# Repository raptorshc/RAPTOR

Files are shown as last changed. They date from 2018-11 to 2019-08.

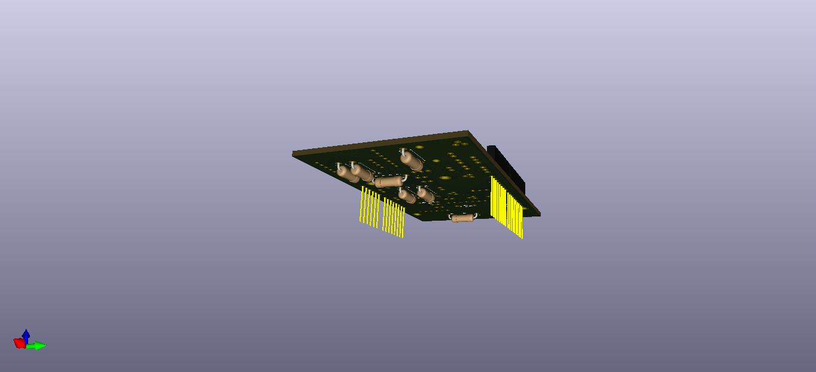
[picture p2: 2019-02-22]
hardware/phoneix_3D_bottom.png

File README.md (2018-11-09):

# RAPTOR

The Ram-Air Parafoil Targeted Object Return (RAPTOR) system is an autonomous payload designed for the simplification of high-altitude balloon payload recovery.

The project aims to alter final landing location by deflecting an attached parafoil. An Arduino Uno will control two servos that can trim the parafoil's brake lines to change course.  

This repository contains all of the flight code used for the project, flight data collected and analyzed, and simulation files.

## 1. Payload Design Overview

The RAPTOR payload will contain a few consistent components across all iterations of the payload. The box is a simple styrofoam box, the exterior of which will be modified to hold servo housings. Inside of the box is the electrical components and sensors to drive the payload. The "brain" of the payload is an Arduino, which will both interact with environmental sensors and drive the outputs.

Every iteration of the payload must be able to fly on regular balloon flights with little to no matenience needed. With these major design considerations in mind, we will set out to build a reliable and reusable payload that can easily be attached to any payload line.

With iterative design in mind, our goal is to make each step simple and elegant. Thus, if there is an easier solution to a problem, we will take that. The goal is to add complexity only as needed over time.

## 2. Flight Software Design

The requirements for flight software are to maintain accurate measurements from a variety of sensors, be able to determine and make the necessary corrections to the flight path, and facilitate the safe descent of the payload train to the ground when over the landing zone.

## 3. Payload Iterations

### **Kestrel**

'Kestrel' is part of the naming convention chosen for RAPTOR as it goes through various design and developement stages. Kestrel is the smallest raptor in North America, and was chosen to represent RAPTOR's first iteration, or the '0.5' version of the project.

Kestrel was designed and built to be a testing payload, where we could fly our environmental sensors, continuous servos and solenoids to test their reliability and power consumption on a high altitude flight.

![alt text](https://lh3.googleusercontent.com/1o9nY4RvOQGDZTQBY0d3M0oymKL5FPMcOie_QyGTn0_0s2nfabPlYtp4XrS53vgEl31j4T295NOKGKeISqotcockGwPX17MacXHBMp5uQQhCgSTBN3fivYLe4FH1sv7LIwD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 "Kestrel Payload")

![alt text](https://lh3.googleusercontent.com/uCabqWDjVLErh2zyCXdYhAvNTMVmv-jxHRv1PDopmbwNDc_ZhoJPY0nD8ILytu6s-EueVPPUXQ7v6TyP5FRkylkzkazS8X3QIo4R5wyPkX31q6gQq4APF3gKN9XSp_Dt44V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 "Kestrel Payload Interior Pre-Flight")

### **Falcon**

'Falcon' is the '1.0' version of the project. Falcon began when we made a completely new payload, with the plan of making our first real guided flight in mind. This is the first iteration of the payload with the parafoil attached, where all of the major flight goals for the project will be achieved. These goals include cut down, parafoil deployment, and guided descent.

![alt text](https://lh3.googleusercontent.com/08VQK_cJHctBsdPiarJFAllG-HUXjV4KG93Qopkh8PWqxyemp60GxGwwhsPvioKC6TSWX8pKGrXxwrKrk8XXFop7fkjdXXR2VQqJoVmNaJoeIMKOxXNGcJJWGRxl6ngI7tU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 "Falcon Payload with Parafoil Attached")

![alt text](https://lh3.googleusercontent.com/nTsq8ke9CdPrCzIl53acNa8SwdOpLuPSAk6aUb3CXytfzZnTHvZFV9xw1yQSyBJqHkr0cgnZ6tlVB8Kzcdpo9wiceyWq20kCEg2xDIhHhK3iLWAF6V_QYCNNu1fWfUKg2jk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 "Interior of Payload Pre-Flight")

![alt text](https://lh3.googleusercontent.com/qpwUnisi4AMiziGQZmHzRLYBiRqKub_Wn9nlaQfpf05oFm5Ekyx_R4OeDEhFKlS7zY80K_rwTjstmUsjaqJ_f78QGzWcw0SdS9lvnNbavl9Xdq8MnOOZnSqH13_WAorVAF_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 "Falcon Payload During Testing")

#### *Falcon Testing*

[Parafoil Testing with Fake Load](https://photos.google.com/share/AF1QipOYNhcAF_VKSpH8EsGm9p09tWBEW8-P44Ib4esdOKR__pPn4U8IfVZbABBhkwzWkA/photo/AF1QipNYzDb1yor08mGMRFYyb5cecjjzEDNiWGI3c_8m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)

[Cutdown and Parafoil Deployment Testing](https://photos.google.com/share/AF1QipOYNhcAF_VKSpH8EsGm9p09tWBEW8-P44Ib4esdOKR__pPn4U8IfVZbABBhkwzWkA/photo/AF1QipNU7GBOfcRdJiM-u27gPR9Wuxxhj8X0IvZJd2tQ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)

[Parafoil Brake Line Servo Test](https://photos.google.com/share/AF1QipOYNhcAF_VKSpH8EsGm9p09tWBEW8-P44Ib4esdOKR__pPn4U8IfVZbABBhkwzWkA/photo/AF1QipONFaLqnrI26lueZZusB5zbdpsSCUT9ZnrO1FEE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)

[Parafoil Controlled Deflection Testing](https://photos.google.com/share/AF1QipOYNhcAF_VKSpH8EsGm9p09tWBEW8-P44Ib4esdOKR__pPn4U8IfVZbABBhkwzWkA/photo/AF1QipOjYvH4XpJ5j8LqXkNAdmoZCI6CpGh4pJOYzDQ6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)

## 4. Flight Reports

### **KESTREL**

#### **April 21, 2018** (UAH Space Hardware Club BalloonSat Flight 75)

Our first flight took the Kestrel payload up to 100,000ft, where the components performed nearly perfectly, with only three measured failures of a solenoid. The following graphs are constructed from the data collected during the flight.

![alt text]( https://lh3.googleusercontent.com/BemMeG_wjjgEnfAlytIrjKeVrs0k2_3DL499e8Ap5Oft2oVPp0bTjnTxFLzm9G5_wCgSZQKKXPSeFjSZQ_YwVKfhydMyssC7hJiGl_VFefC5Ld4zEoicfH3cAaqB6fmjJgo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 "Pressure vs Time, with Solenoid Failure Markings")

![alt text](https://lh3.googleusercontent.com/KNZ6x_Vac3x1Pnvgrhe8NedKYn2VLNuSEfFBFWm-Lp36aQMo7iNe9pHYzUXd3TR03b9J4sRoP69VhWtRAomjtsnrsVQ_ZSnNuRpuq2FJL7O_-B3BK03cpRlcjrfZnnfZXRX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 "Temperature vs Time, with Solenoid Failure Markings")

![alt text]( https://lh3.googleusercontent.com/LbfyWvzu6PWR8G42ObNfinUGaMZgHTH2ggLDe802Y7b2Mt4PNNAm9G_F5JisICvvmlPLEjyTsWcb9FliGdE-NDNIIxiNTZ3leAKVSWQcmAyk3ySunhAUJf4kC4v4u73iBjN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 "Team Photo")

Additional photos: https://photos.app.goo.gl/y1GM2Ua3seM8kpAX6

#### **August 31, 2018** (UAH Space Hardware Club BalloonSat Flight 77)

For our second flight we gathered additional data using the Kestrel payload. A major issue during the flight was that the Arduino power cycled while near the apogee of the flight. Due to a mistake in the code, a baseline pressure is taken when the board initializes, so the altitude during descent tended into the negative values. The following graphs show adjusted data from the flight for ascent. There were no recorded solenoid failures during the flight.

![alt text]( https://lh3.googleusercontent.com/MRX_bFXJetOg1aB5wNyvmU14bfMBnIYrwlvbJ33pcFYwK6eS6S0-DdBDFQAEzepfaU3I5fB7g92ceOtPr6XYwi1YCWP-x7m_2AGui4MWdTZrSNywGwxau3owqjKPpeeZUny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 "Temperature and Altitude vs Time")

![alt text](https://lh3.googleusercontent.com/Y4CDoAoS2dIhLRWhnF7a5mxLAkN89WYJ-2H63kcUrKUIaF_1hElJlrU4Xk-xMh04kAqPIyo8T-RROAUbGWmkpqQO6P9UKqv96oe9mTNt2_tanveFWIan3q2ELKeRTuSr3td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 "Temperature and Pressure vs Time")

### **FALCON**

#### **October 6th, 2018** (UAH Space Hardware Club BalloonSat Flight 78)

Our flight on October 6th, 2018 was the first flight of RAPTOR payload Falcon. The intent of the flight was to fly on the UAH SHC One Month flight and cutdown from the payload train at 800 feet. Upon release from the payload train, the payload would drop 25 feet and deploy a parafoil, beginning guidance toward a designated landing point.
Payload Falcon was the second from the top payload on the flight train, just below the master cutdown and above of all of the other payloads. The intention being that Falcon would release prior to the master cutdown altitude of 1000 feet and after the other payloads had released from the line at 500 feet, clear from our flight path.

During the flight, Falcon successfully released from the payload train at 800 feet; however, as it fell from the payload train it got caught on the parachute bag of the payload directly beneath Falcon. After Falcon got caught on the parachute bag, it was entangled and proceeded to fly with the payload train until the master cutdown released from the balloon. Falcon then fell under the influence of the master cutdown’s parachute and was recovered safely.

Post flight, through inspecting GoPro footage and recorded telemetry, it was clear that Falcon successfully released from the payload train and deployed the parafoil; however, it was simply entangled in the parachute bag. Even though Falcon became entangled, there was still several takeaways from the flight.

First we learned that both the balloon and parafoil release mechanism worked correctly. We proved that the electronics were able to power and sustain a short flight, we showed that the coding was able to cycle through all of the flight states correctly. We also found that the GPS receiver was reporting altitude in MSL instead of AGL, which could have negative effects on future flights. Data recorded to the SD card was formatted incorrectly, making it difficult for post-flight analysis. Finally, we learned that our flight checklist was missing several steps, including how to properly start the GoPro cameras.

![alt text](https://lh3.googleusercontent.com/LHJe6HiXcIz81Ea09SGUOwY1y3NmHhyFWJHuItK7zjxrx4ana2Pq6K-i-WVNmY_tG5ZWHFH_c-4tZLxe9ZF3UkqxDCNr89Ehnhs_neyA-6rPpHWl1EMa-16J-t3yzjn635y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 "Team Photo")

Additional photos: https://photos.app.goo.gl/wStjm3jxJ4gyiKRt6

#### **October 27th, 2018** (UAH Space Hardware Club BalloonSat Flight 79)

For our flight on October 10th, 2018, we flew the RAPTOR payload Falcon for the second time. The intent of the flight was to fly on a balloon up to 1000 feet and then release from the balloon. Upon release from the balloon, the payload would drop 10 feet and release a parafoil, beginning guidance toward a designated landing point.

Payload Falcon did not successfully release from the balloon line. Instead it remained attached and flew with the balloon until the balloon’s bursting altitude of approximately 80,000 feet. Upon burst, the payload free-fell until 990 feet and deployed the parafoil, which due to the elevation of the landing sight - was only 300 feet above the ground. The parafoil released from the payload correctly; however, it became entangled in the still-attached balloon line. Although the parafoil was tangled, it slowed the payload down enough that the payload landed safely and was recovered fully intact.

Post flight, through inspecting GoPro footage and the balloon release mechanism, it was discovered that the small line connecting the payload to the balloon line twisted so tightly around the balloon release mechanism release wheel, that the friction between the line and release wheel kept the payload attached to the balloon. In both the video and recorded telemetry data, the release mechanism solenoid was triggered correctly by the Arduino microcontroller.

![alt text](https://lh3.googleusercontent.com/DX8jpagSZ6LKXMaGTUnuR-Gp7IC6Lo57QNAOB3CmmnxLZm5vVSMHzMlLcpr2Hw_cCj3_YJ5Pzvy5XdEeT8kTMvjd3I0hRwUJ8NQtbs2XuicFXm1EfYEKwcU-171ZV9Z0B54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 "Team Photo")

_The small brown line twisted around the mechanism’s paw very tightly._

Even though the payload did not release from the balloon and controlled flight was not achieved, there were still several takeaways from the flight.
First, we learned that the balloon release could fail when the connecting line twisted too many times. We also learned that there was a software design flaw that caused the Arduino to stop writing data to the SD card when the payload was higher than the release altitude. While not intended, we found that our payload is able to fly to high altitudes, not suffer from dropping temperatures, and has enough power to last the duration of the flight. We also learned that, unlike our payload, GoPro cameras can freeze-up at high altitude. On our flight, this caused them to fail and shut down after only ~30 minutes into the flight. Finally, we learned that the parafoil can be safely deployed at terminal velocity (although not ideal) and that the payload box is strong enough to sustain a fast landing.

![alt text](https://lh3.googleusercontent.com/Aypx76Ql5LVa8p2PFBuOJys9CJ3AVa-NEbSdwvvvx31Qhf6bkzXBJTn4RS2yL9QKpeO0D3fYkl0NPFLIo-4bcgZaK_JbQFQ9Q29sOfMKvP4cvz1yX0B2EHW416THLgJkycu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 "Team Photo")

Additional photos: https://photos.app.goo.gl/nkUsBDCjjpgs3n9UA

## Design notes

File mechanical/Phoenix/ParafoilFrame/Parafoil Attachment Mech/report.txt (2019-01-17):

Report Name: C:\Users\lsp00\Documents\Raptor\raptor\mechanical\Phoenix\ParafoilFrame\Parafoil Attachment Mech\report.txt
Report Time: 1/14/2019 8:52:06 PM
Report Options:
    Part Names

Select Set #1:
    3ft skeleton.par:2
    Parafoil_Pin_Mount V2.par:1
    Parafoil_Pin_Mount V2.par:4
    Parafoil Belly Surface.par:1
    45degree Support Bar.par:3
    Parafoil_Rod_Mount V2.par:2
    Short_Center_Dowel.par:1
    Quarter Diamter Dowel.par:2
    45degree Support Bar.par:2
    Coupler.par:2
    Long_Center_Dowel.par:2
    3ft skeleton.par:1
    Parafoil_Rod_Mount V2.par:1
    Short_Center_Dowel.par:2
    Duct Tape.par:2
    Parafoil_Pin_Mount V2.par:3
    Parafoil_Pin_Mount V2.par:2
    Parafoil_Rod_Mount V2.par:4
    Quarter Diamter Dowel.par:1
    Duct Tape.par:1
    Long_Center_Dowel.par:1
    PDRPayloadv1.par:1
    45degree Support Bar.par:1
    Parafoil_Rod_Mount V2.par:3
    Coupler.par:1
    45degree Support Bar.par:4

Interferences:
    1 of 15
    3ft skeleton.par:2
    Duct Tape.par:2

    2 of 15
    3ft skeleton.par:2
    Duct Tape.par:1

    3 of 15
    Parafoil_Pin_Mount V2.par:1
    PDRPayloadv1.par:1

    4 of 15
    Parafoil_Pin_Mount V2.par:4
    Short_Center_Dowel.par:2

    5 of 15
    Parafoil Belly Surface.par:1
    Parafoil_Pin_Mount V2.par:3

    6 of 15
    Parafoil Belly Surface.par:1
    Parafoil_Pin_Mount V2.par:2

    7 of 15
    45degree Support Bar.par:3
    Short_Center_Dowel.par:1

    8 of 15
    Short_Center_Dowel.par:1
    45degree Support Bar.par:2

    9 of 15
    Short_Center_Dowel.par:1
    Long_Center_Dowel.par:2

    10 of 15
    Short_Center_Dowel.par:1
    Parafoil_Pin_Mount V2.par:3

    11 of 15
    Short_Center_Dowel.par:1
    Long_Center_Dowel.par:1

    12 of 15
    Long_Center_Dowel.par:2
    Short_Center_Dowel.par:2

    13 of 15
    Short_Center_Dowel.par:2
    Long_Center_Dowel.par:1

    14 of 15
    Short_Center_Dowel.par:2
    45degree Support Bar.par:1

    15 of 15
    Short_Center_Dowel.par:2
    45degree Support Bar.par:4

    15 Interferences Detected

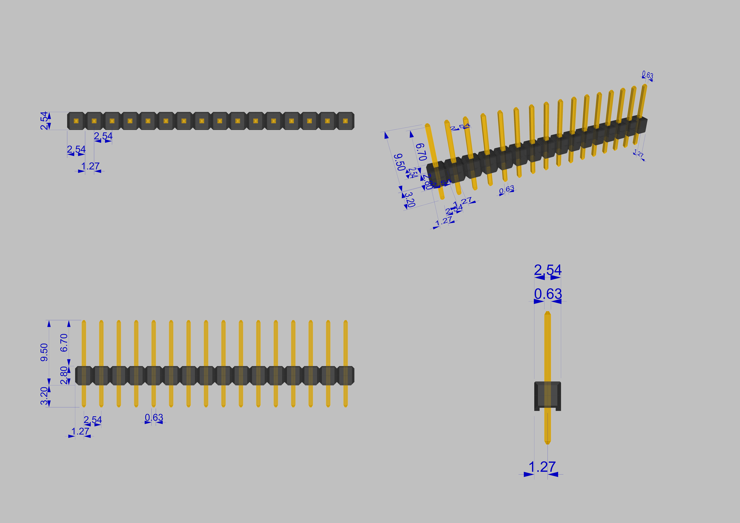
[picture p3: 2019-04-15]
hardware/RAPTOR/Renderings/PinHeadersDim SF2014.jpg

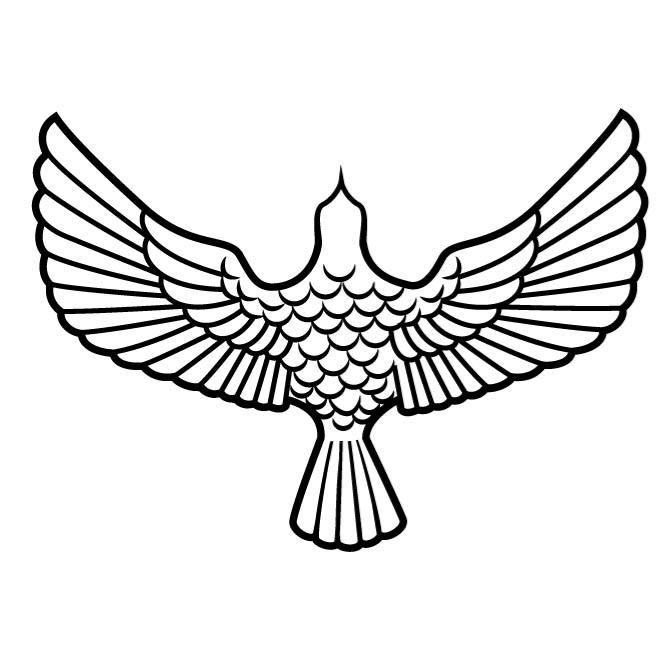
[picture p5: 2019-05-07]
hardware/Phoenix.png

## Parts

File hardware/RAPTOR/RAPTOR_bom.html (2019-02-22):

Ref | Qnty | Value | Part | Datasheet | Description | Vendor
BT1 | 1 | 7.4V | Device:Battery | ~ | Battery (multiple cells)
BZ1 | 1 | Buzzer | Device:Buzzer | ~ | Buzzer, polar
C1, C2 | 2 | 0.33 uF | Device:C | ~ | Unpolarized capacitor
C3, C4 | 2 | 0.1uF | Device:C | ~ | Unpolarized capacitor
D1 | 1 | LED | Device:LED | ~ | LED generic
D2, D4, D7 | 3 | SOLP_LED | Device:LED | ~ | LED generic
D3, D5, D6 | 3 | SOLC_LED | Device:LED | ~ | LED generic
M1, M2 | 2 | Motor_Servo | Motor:Motor_Servo | http://forums.parallax.com/uploads/attachments/46831/74481.png | Servo Motor (Futaba, HiTec, JR connector)
P1 | 1 | Power | Connector_Generic:Conn_01x08 |  | Generic connector, single row, 01x08, script generated (kicad-library-utils/schlib/autogen/connector/)
P2 | 1 | Analog | Connector_Generic:Conn_01x06 |  | Generic connector, single row, 01x06, script generated (kicad-library-utils/schlib/autogen/connector/)
P3 | 1 | Digital | Connector_Generic:Conn_01x10 |  | Generic connector, single row, 01x10, script generated (kicad-library-utils/schlib/autogen/connector/)
P4 | 1 | Digital | Connector_Generic:Conn_01x08 |  | Generic connector, single row, 01x08, script generated (kicad-library-utils/schlib/autogen/connector/)
P5, P6, P7, P8 | 4 | CONN_01X01 | Connector_Generic:Conn_01x01 |  | Generic connector, single row, 01x01, script generated (kicad-library-utils/schlib/autogen/connector/)
Q1, Q2, Q3, Q4 | 4 | MOSFET-NCH-2N7002PW | SparkFun-DiscreteSemi:MOSFET-NCH-2N7002PW
SW1 | 1 | EEPROM_BTN | Switch:SW_SPST |  | Single Pole Single Throw (SPST) switch
SW2 | 1 | SOLP_SW | Switch:SW_SPST |  | Single Pole Single Throw (SPST) switch
SW3 | 1 | SOLC_SW | Switch:SW_SPST |  | Single Pole Single Throw (SPST) switch
U1 | 1 | BMP280 | RAPTOR-rescue:BMP280-bmp280
U2 | 1 | BNO055 | RAPTOR-rescue:BNO055-bno055
U3 | 1 | OpenLog | RAPTOR-rescue:OpenLog-openlog
U4 | 1 | AdafruitGPS | RAPTOR-rescue:AdafruitGPS-adafruitgps
U5, U6 | 2 | L7805 | Regulator_Linear:L7805 | http://www.st.com/content/ccc/resource/technical/document/datasheet/41/4f/b3/b0/12/d4/47/88/CD00000444.pdf/files/CD00000444.pdf/jcr:content/translations/en.CD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 | Positive 1.5A 35V Linear Regulator, Fixed Output 5V, TO-220/TO-263/TO-252
U7 | 1 | U3V12F12 | RAPTOR-rescue:U3V12F12

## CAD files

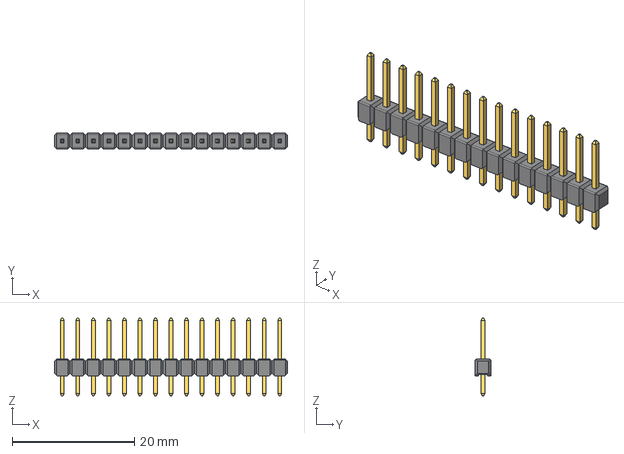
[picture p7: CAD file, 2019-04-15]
hardware/RAPTOR/PCB CAD/Pin Header 1x15 TH Pitch 2.54mm.stp
38.1 x 2.54 x 12.7 mm

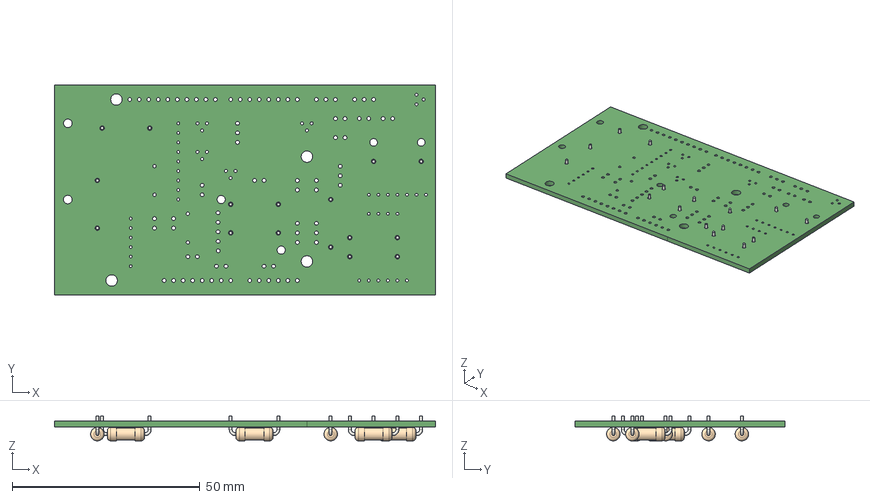
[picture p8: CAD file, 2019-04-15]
hardware/RAPTOR/RAPTOR.step
101.6 x 55.9 x 6.60 mm
Socket_header_Arduino_1x08 x 2
Socket_header_Arduino_1x06
Socket_header_Arduino_1x10

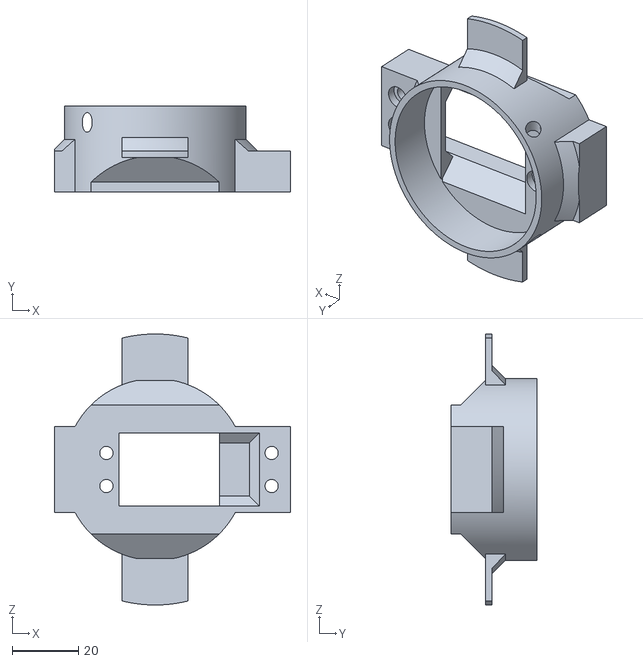
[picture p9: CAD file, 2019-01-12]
mechanical/Falcon/Drag line controller update/v3/Motor and Wheel Frame NO SUPORRT.stl
71.5 x 26.1 x 82.0

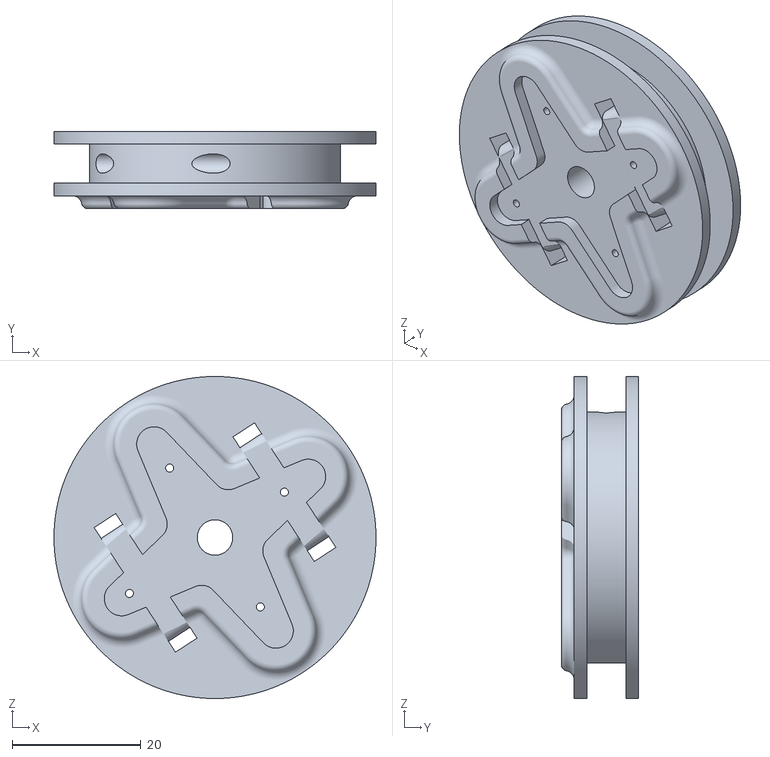
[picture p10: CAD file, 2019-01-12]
mechanical/Falcon/Drag line controller update/Wheel.stl
50.0 x 12.0 x 50.0

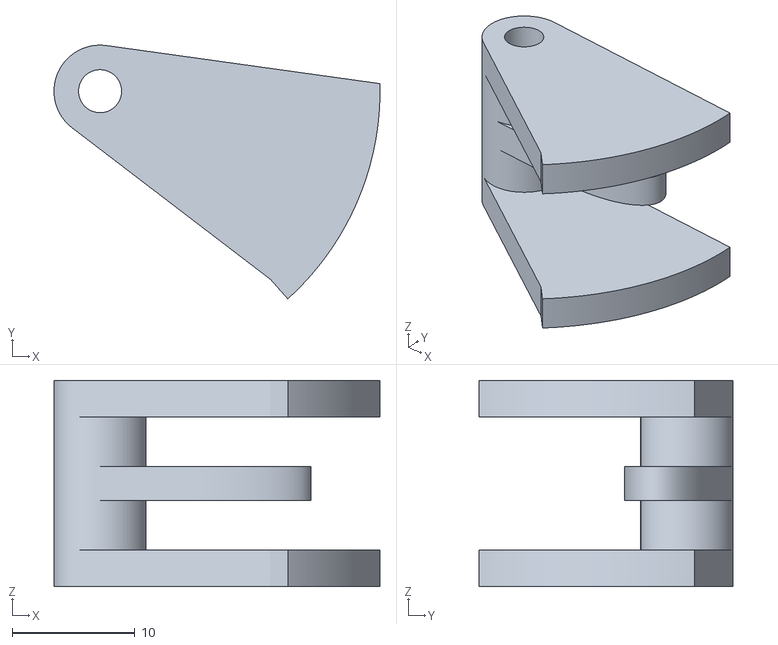
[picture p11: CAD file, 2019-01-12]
mechanical/Falcon/Release Mechanism Redesign/NoStickWeel.stl
26.5 x 20.7 x 16.8

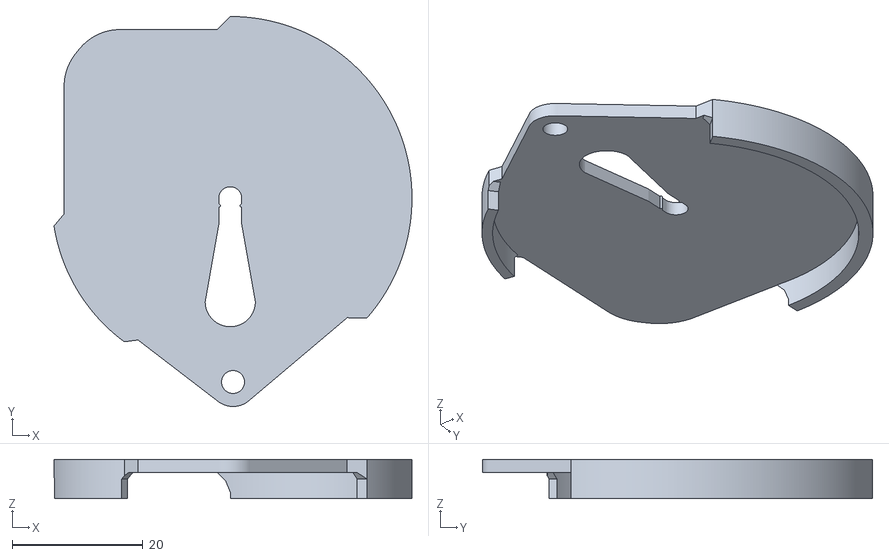
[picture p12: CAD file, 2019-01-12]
mechanical/Falcon/Release Mechanism Redesign/v4/Top Frame.stl
54.7 x 59.6 x 6.00

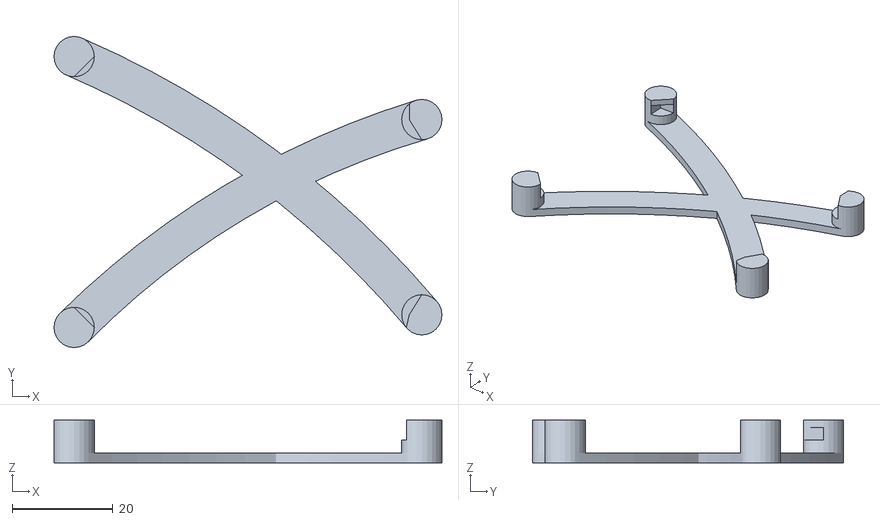
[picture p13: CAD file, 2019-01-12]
mechanical/Phoenix/BoardMounts/Arduino_Uno_bumper_fixedV2.0.stl
77.0 x 61.7 x 8.50

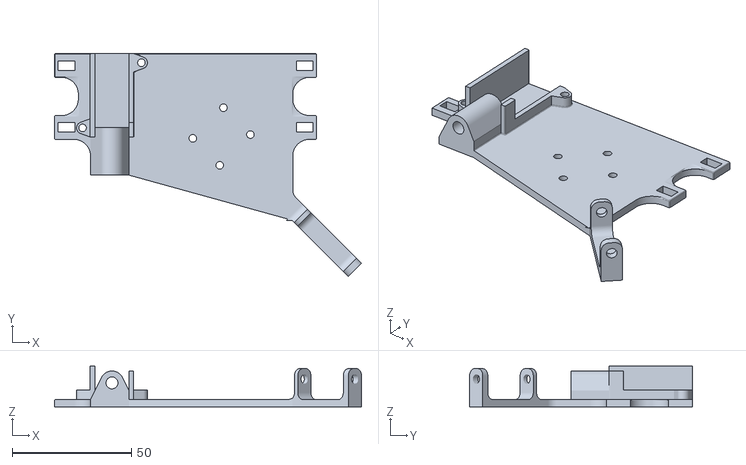
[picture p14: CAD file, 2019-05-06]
mechanical/Phoenix/ReleaseMechanisms/PrimaryArcheryRelease/Base_4.stl
128.8 x 93.5 x 17.0

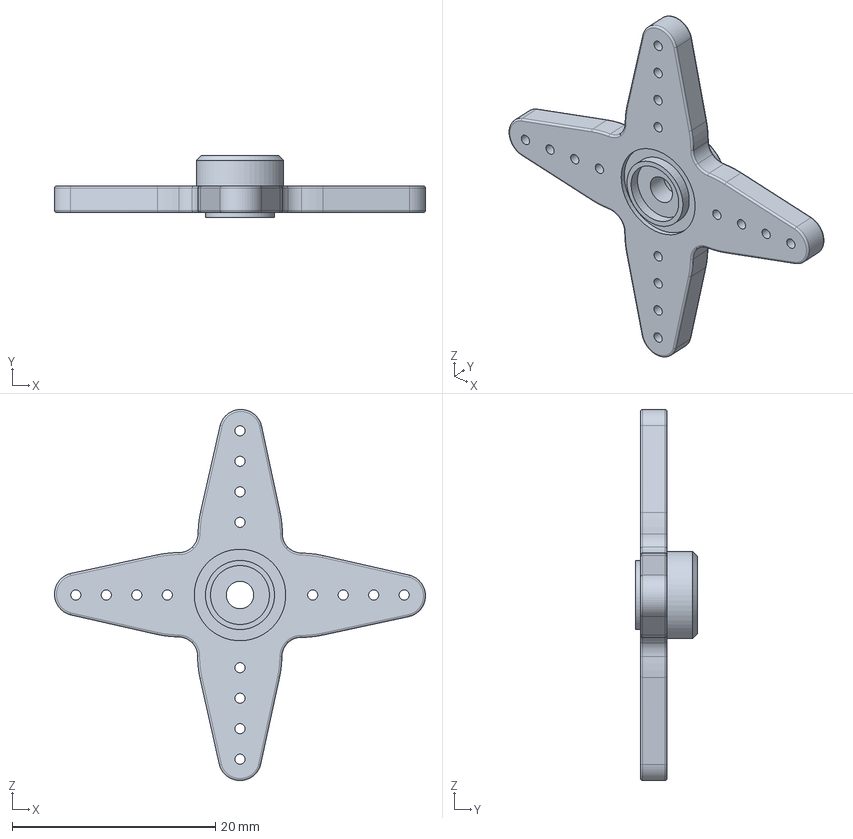
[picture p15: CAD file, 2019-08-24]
mechanical/Phoenix/ServoMount/SingleServoMount/FutabaS3003/Axis-holder v2.step
36.5 x 6.10 x 36.5 mm

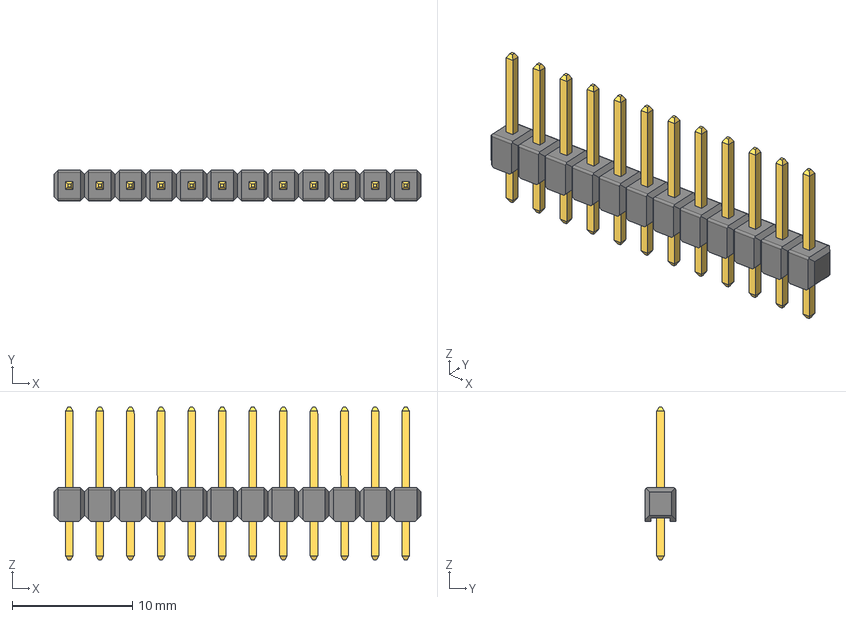
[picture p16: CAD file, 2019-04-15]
hardware/RAPTOR/PCB CAD/Pin Header 1x12 TH Pitch 2.54mm.stp
30.5 x 2.54 x 12.7 mm

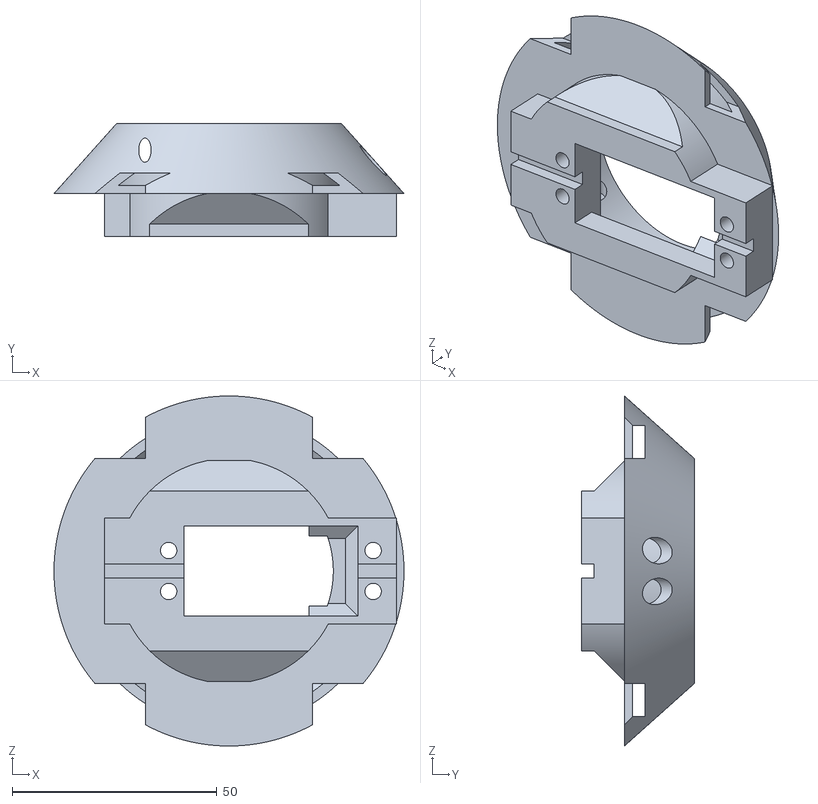
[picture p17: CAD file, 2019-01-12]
mechanical/Falcon/Drag line controller update/Chamfer Edge UpgradeMotor and Wheel Frame NO SUPORRT.stl
85.6 x 27.6 x 85.6

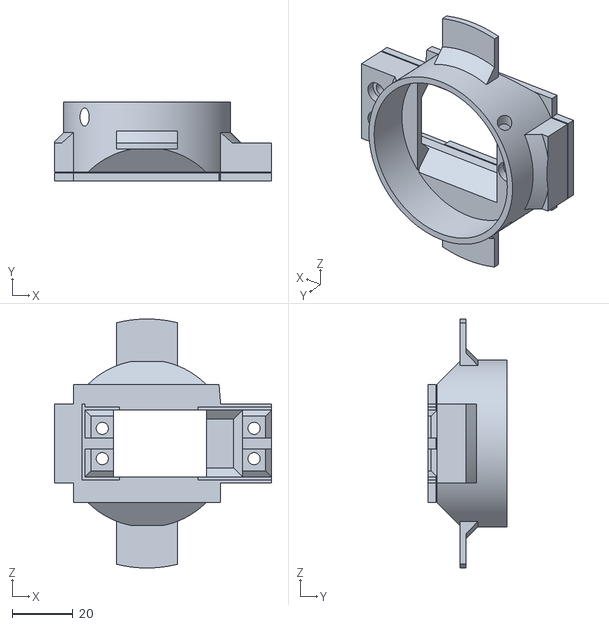
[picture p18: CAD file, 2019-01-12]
mechanical/Falcon/Drag line controller update/v3/Motor and Wheel Frame.stl
71.5 x 26.1 x 82.0

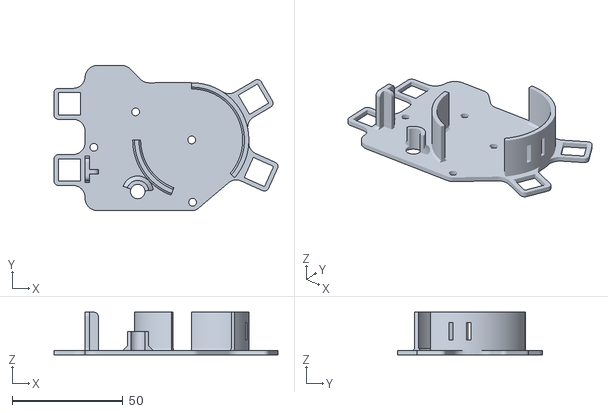
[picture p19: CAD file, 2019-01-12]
mechanical/Falcon/Release Mechanism Redesign/v4/Frame.stl
101.0 x 65.4 x 19.2

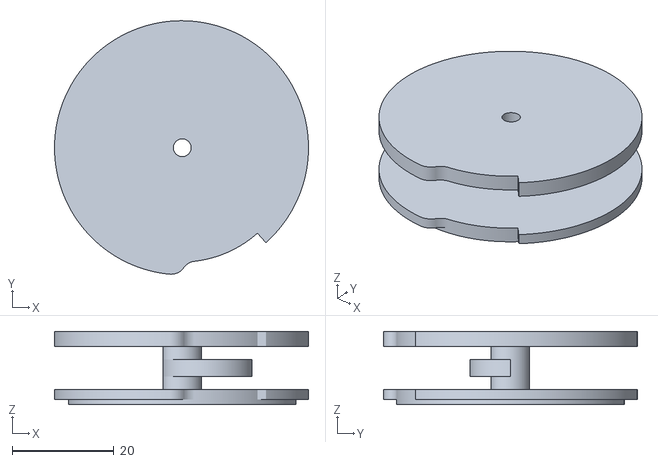
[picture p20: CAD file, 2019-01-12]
mechanical/Falcon/Release Mechanism Redesign/Wheel.stl
50.0 x 49.9 x 14.4

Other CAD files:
mechanical/Phoenix/ServoMount/Wheel.stl
mechanical/Phoenix/ReleaseMechanisms/PrimaryArcheryRelease/tensionPart.stl
mechanical/Phoenix/ServoMount/Chamfer Edge UpgradeMotor and Wheel Frame NO SUPORRT.stl
mechanical/Phoenix/ServoMount/SingleServoMount/FutabaS3003/Servo Futaba S3003 v6.step
hardware/RAPTOR/PCB CAD/Pin Header 1x1 TH Pitch 2.54mm.stp
hardware/RAPTOR/PCB CAD/Pin Header 1x10 TH Pitch 2.54mm.stp
hardware/RAPTOR/PCB CAD/Pin Header 1x11 TH Pitch 2.54mm.stp
hardware/RAPTOR/PCB CAD/Pin Header 1x13 TH Pitch 2.54mm.stp
hardware/RAPTOR/PCB CAD/Pin Header 1x14 TH Pitch 2.54mm.stp
hardware/RAPTOR/PCB CAD/Pin Header 1x16 TH Pitch 2.54mm.stp
hardware/RAPTOR/PCB CAD/Pin Header 1x2 TH Pitch 2.54mm.stp
hardware/RAPTOR/PCB CAD/Pin Header 1x3 TH Pitch 2.54mm.stp
hardware/RAPTOR/PCB CAD/Pin Header 1x4 TH Pitch 2.54mm.stp
hardware/RAPTOR/PCB CAD/Pin Header 1x5 TH Pitch 2.54mm.stp
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

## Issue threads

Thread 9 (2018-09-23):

Skynet Vector Issue

seaan, 2018-09-23:
Arduino doesn't support vectors! Need to re-implement using something else.

kdaigle95, 2018-10-15:
Fixed by ArduinoSTL library.

Closed 2018-10-15.

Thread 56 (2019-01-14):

Motor + Buzzer Wrong Voltage

seaan, 2019-01-14:
At 6V should be 5V

Closed 2019-01-15.

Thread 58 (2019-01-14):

Pulldown Resistors on Switches

seaan, 2019-01-14:
"You've got several switches between +5V and GPIO pins. Is the intent to detect when the switch is pressed? If so, you need to put a pull-down resistor on the associated GPIO pins; otherwise they'll be left floating and could vary randomly between HIGH and LOW

- You can do a physical pulldown resistor in your schematic, or enable internal pullup resistors on the ATMega. If you do the latter, you will need your switch to connect to GND instead of VCC
- Failure to do this is a potential cause of "spooky" errors that occur in some situations but not others. You spend forever looking for a software problem that turns out to have been caused by static electricity or something"

Closed 2019-01-15.

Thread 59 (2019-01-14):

Change Net Names from Numbers

seaan, 2019-01-14:
"I don't recommend using numbers for your net names, because it makes it really confusing when Arduino pin 1 connects to net 7 which connects to pin 2 on a switch. It's better to use names for your nets, like "EEPROM_reset" or something of that nature"

Closed 2019-01-15.

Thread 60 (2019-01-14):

Check MOSFET Current Draw

seaan, 2019-01-14:
"Your MOSFETs don't seem to be rated for much current draw (310 mA). Is that firmly above what the solenoid draws? Note that the solenoid current draw will spike when initially turned on, then settle into a lower steady state draw"

seaan, 2019-01-15:
checked, solenoid is 250mA we good fam

Closed 2019-01-15.

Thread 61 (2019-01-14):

Connect INT pin BNO055

seaan, 2019-01-14:
"Not sure how high your data rates need to be, but you can simplify your programming for high-rate IMU measurements by connecting the INT pin on the BNO055"

seaan, 2019-01-15:
ran out of interrupt pins, don't need that high data rate from IMU so we're good.

Closed 2019-01-15.

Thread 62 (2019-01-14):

Mount the Entire IMU

seaan, 2019-01-14:
"For the IMU, you actually should physically connect all of the pins, or at least the pins in the corners. When you only attach the pins on one side you've made a little cantilevered structure that is very happy to shake. Nbd for your pressure sensor or openlog, but it will superimpose noise upon your IMU data."

seaan, 2019-01-23:
Resolved by #79

Closed 2019-01-23.

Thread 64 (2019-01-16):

Move MOSFET After Components

seaan, 2019-01-16:

seaan, 2019-01-23:
Fixed by #79

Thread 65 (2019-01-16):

Change VRegs to Buck Converters

seaan, 2019-01-16:
Elena insisted.

seaan, 2019-01-23:
Resolved by #79

Closed 2019-01-23.

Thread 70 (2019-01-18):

fix screw hole top right

seaan, 2019-01-18:

Closed 2019-02-02.

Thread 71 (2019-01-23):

Move traces back from the edge of the board

seaan, 2019-01-23:
"Traces really close to the edge of the board, move them back a bit or make the board a little bit bigger, at least like 15 mils or so."

cjo0008, 2019-01-23:
this should be resolved but I want confirmation that it is fine

Closed 2019-02-02.

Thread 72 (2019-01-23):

Off-Board Buzzer

seaan, 2019-01-23:

seaan, 2019-01-26:
resolved by #80

Closed 2019-02-02.

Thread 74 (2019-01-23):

Widen some through holes

seaan, 2019-01-23:

seaan, 2019-01-24:
#80 resolves

Closed 2019-02-02.

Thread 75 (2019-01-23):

Replace signal MOSFETs with power MOSFETs

seaan, 2019-01-23:

Closed 2019-02-02.

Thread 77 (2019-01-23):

Fix silkscreen

seaan, 2019-01-23:

Closed 2019-02-02.

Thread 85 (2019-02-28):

Size of header holes too small

seaan, 2019-02-28:

seaan, 2019-02-28:
resolved by #84

Closed 2019-03-06.

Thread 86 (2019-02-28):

Molex Connector Spacing

seaan, 2019-02-28:

seaan, 2019-02-28:
resolved by #84

Closed 2019-03-06.

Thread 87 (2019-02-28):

MOSFET Style/Hole Spacing

seaan, 2019-02-28:

seaan, 2019-02-28:
resolved by #84

Closed 2019-03-06.

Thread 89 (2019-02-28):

Flip SD Card Reader Holes

seaan, 2019-02-28:

seaan, 2019-02-28:
resolved by #84

Closed 2019-03-06.

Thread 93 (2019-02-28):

Add version to physical pcb

seaan, 2019-02-28:

seaan, 2019-02-28:
resolved by #84

Closed 2019-03-06.

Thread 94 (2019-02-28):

Increase diameter on pin holes for easy soldering

seaan, 2019-02-28:

seaan, 2019-02-28:
resolved by #84

Closed 2019-03-06.

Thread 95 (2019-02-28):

Move IMU to the bottom of the board

seaan, 2019-02-28:

seaan, 2019-02-28:
resolved by #84

Closed 2019-03-06.

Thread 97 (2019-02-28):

Add logical labels to sections

seaan, 2019-02-28:
"these are motors", "these are LEDs"

seaan, 2019-03-06:
resolved by #84

Closed 2019-03-06.

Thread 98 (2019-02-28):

Add button to RX and TX

seaan, 2019-02-28:

seaan, 2019-03-01:
resolved by #84

Closed 2019-03-06.

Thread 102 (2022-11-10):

Not an issue but a question

simon88, 2022-11-10:
Hi,

I'm playing with your code this is a nice project. but for now I have a question. I've seen your a re usin a `BNO055` 9dof module, but in your code your are not use data coming from this sensor why ? All calculations are done with barotemeter and GPS in `pathfinder`, the only place where Ican find `bno` is in `Raptor::print_data()`, there is a raison why you don't use `BNO` datas ?

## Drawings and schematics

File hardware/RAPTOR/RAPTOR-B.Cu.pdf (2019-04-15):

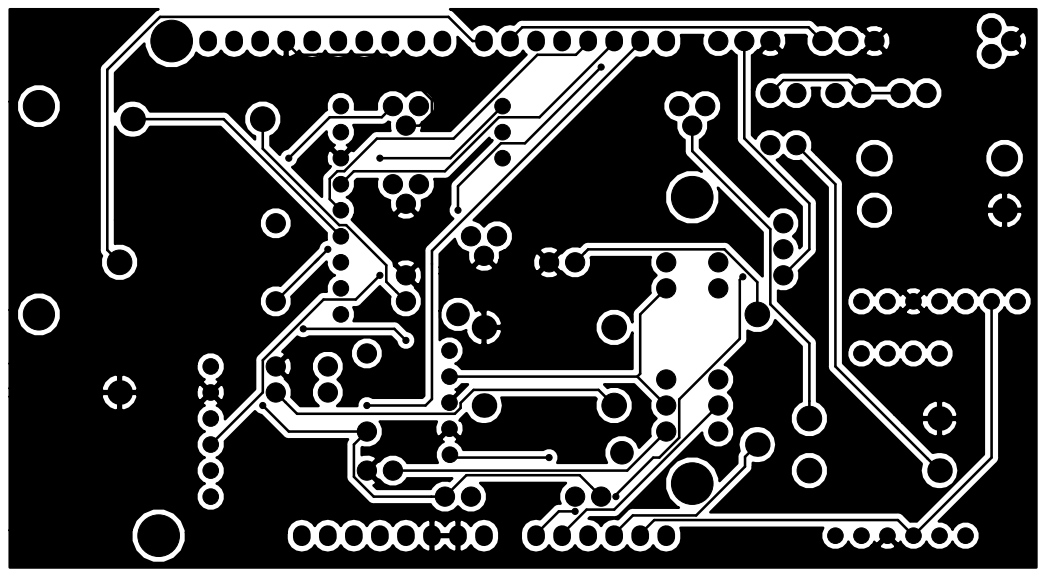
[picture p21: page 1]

File: RAPTOR.kicad_pcb Sheet:
Id: 1/1 Title: RAPTOR PCB

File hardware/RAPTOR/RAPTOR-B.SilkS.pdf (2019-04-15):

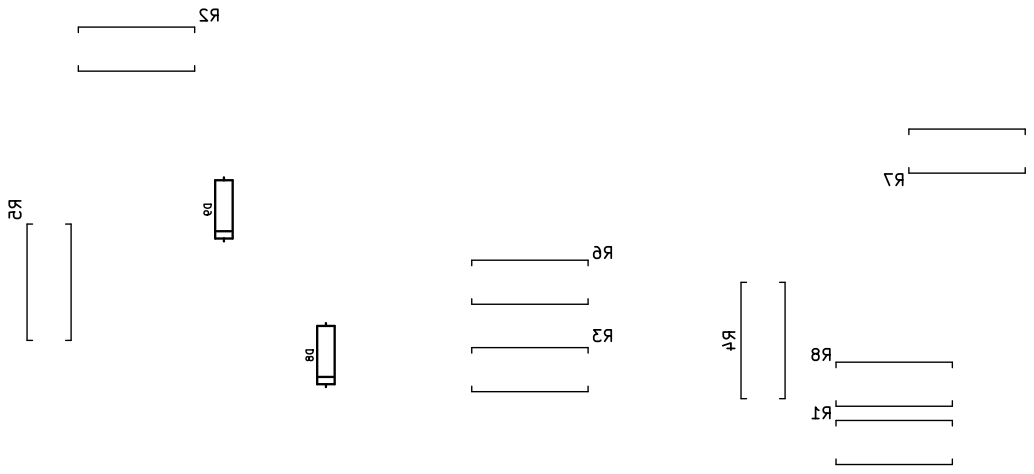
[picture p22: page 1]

Id: 1/1 Title: RAPTOR PCB

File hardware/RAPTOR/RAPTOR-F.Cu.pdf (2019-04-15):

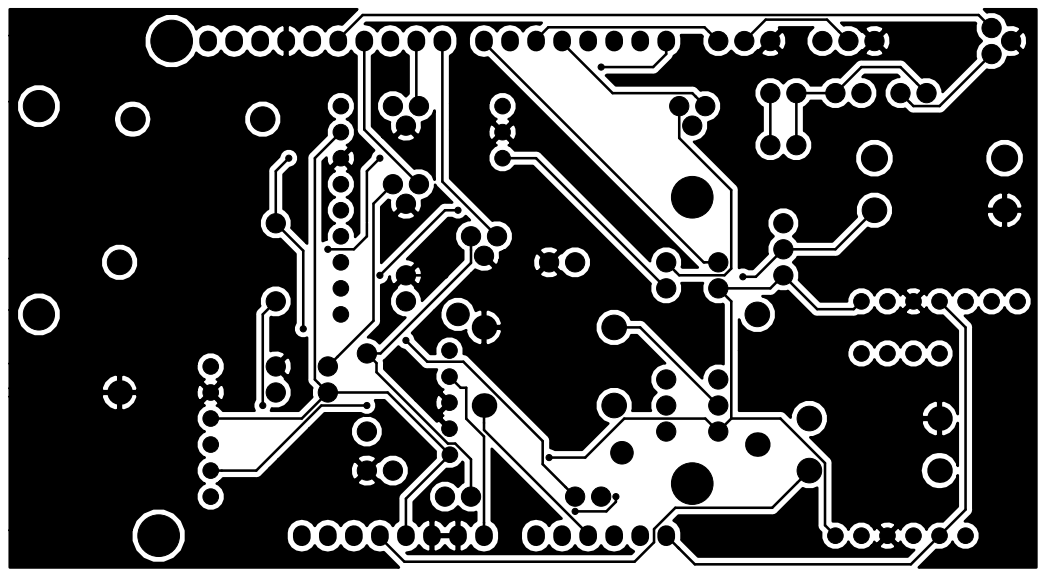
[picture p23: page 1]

File: RAPTOR.kicad_pcb Sheet:
Id: 1/1 Title: RAPTOR PCB

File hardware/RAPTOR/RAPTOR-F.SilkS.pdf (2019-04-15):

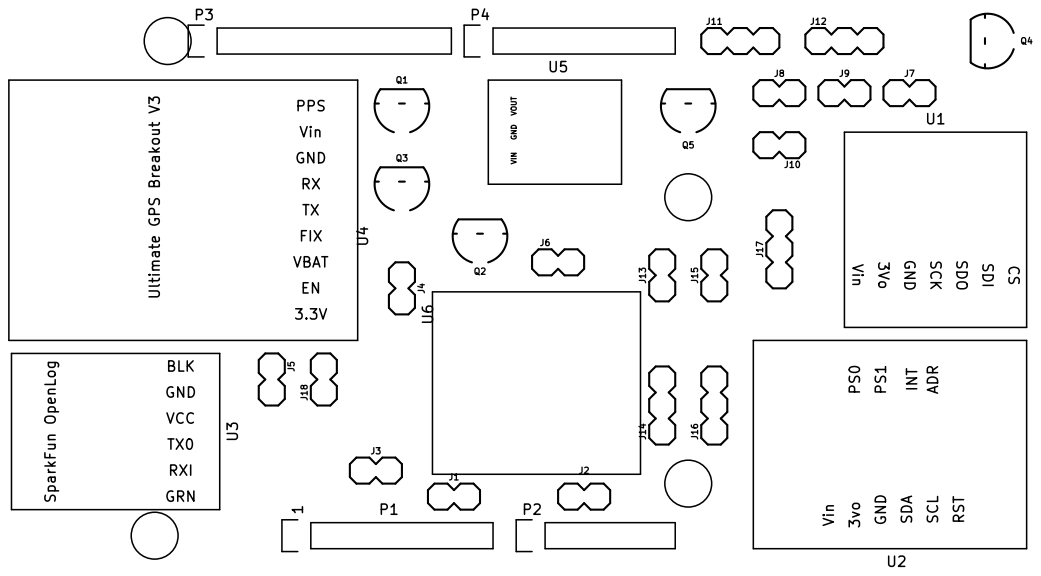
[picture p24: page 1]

1 U5 VOUT GND VIN U1 Vin 3Vo GND SCK SDO SDI CS

Vin PPS Ultimate GPS Breakout V3

File: RAPTOR.kicad_pcb Sheet:
Id: 1/1 Title: RAPTOR PCB

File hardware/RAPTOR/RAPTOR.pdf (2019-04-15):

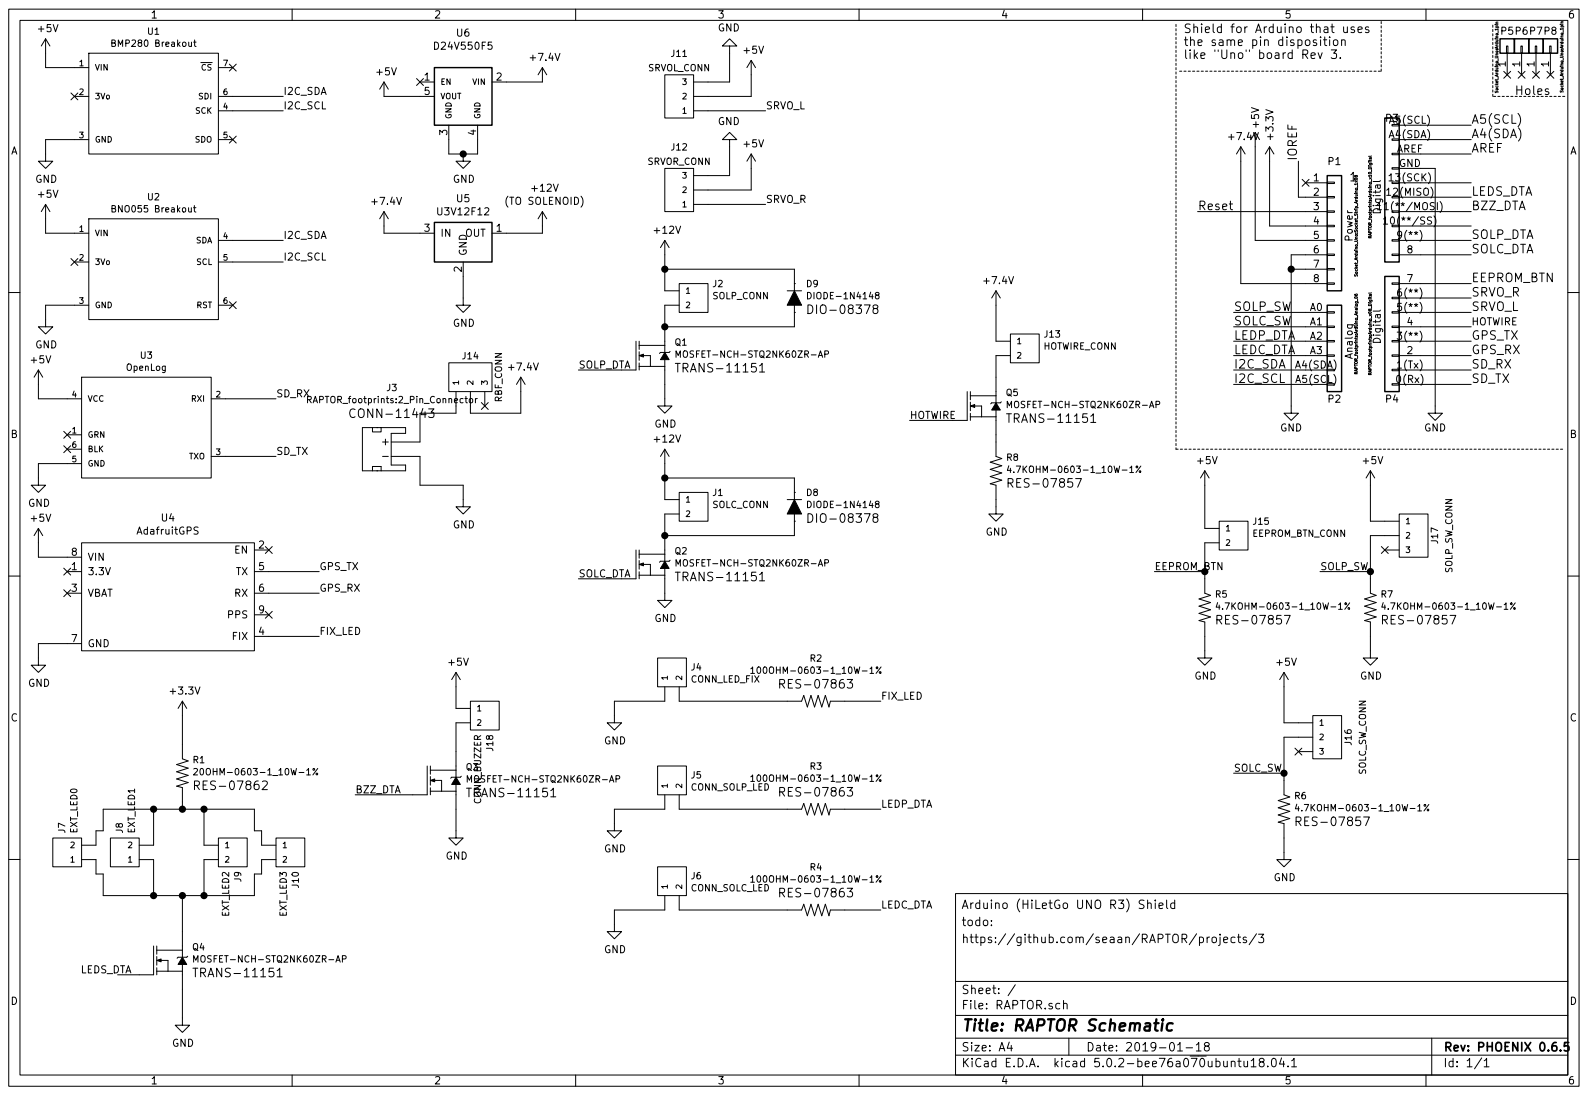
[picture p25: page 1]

A5(SCL)Holes Shield for Arduino that uses
the same pin disposition
like "Uno" board Rev 3. 1

File: RAPTOR.sch Sheet: / https://github.com/seaan/RAPTOR/projects/3

Id: 1/1 Title: RAPTOR Schematic

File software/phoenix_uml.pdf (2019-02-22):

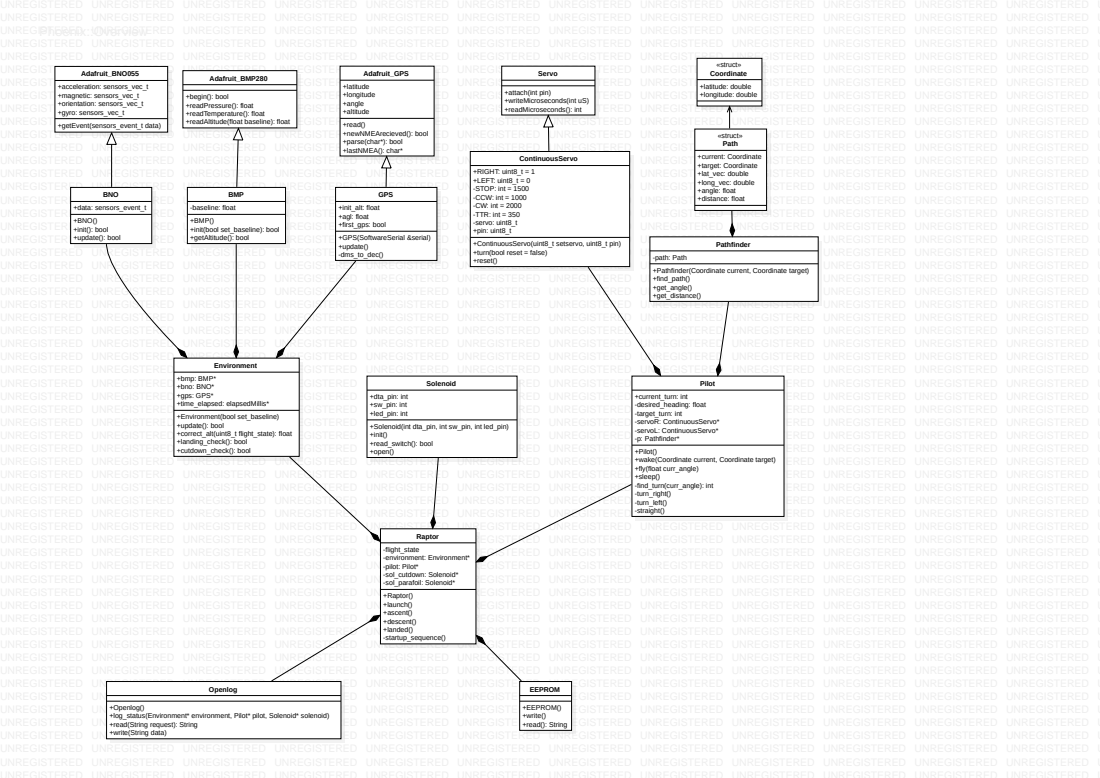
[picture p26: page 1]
UNREGISTERED UNREGISTERED UNREGISTERED UNREGISTERED UNREGISTERED UNREGISTERED UNREGISTERED UNREGISTERED UNREGISTERED UNREGISTERED UNREGISTERED UNREGISTERED UNREGISTERED UNREGISTERED UNREGISTERED UNREGISTERED UNREGISTERED UNREGISTERED UNREGISTERED UNREGISTERED UNREGISTERED UNREGISTERED UNREGISTERED UNREGISTERED UNREGISTERED UNREGISTERED UNREGISTERED UNREGISTERED UNREGISTERED UNREGISTERED UNREGISTERED UNREGISTERED UNREGISTERED UNREGISTERED UNREGISTERED UNREGISTERED UNREGISTERED UNREGISTERED UNRE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

+attach(int pin)
+writeMicroseconds(int uS)
+readMicroseconds(): int

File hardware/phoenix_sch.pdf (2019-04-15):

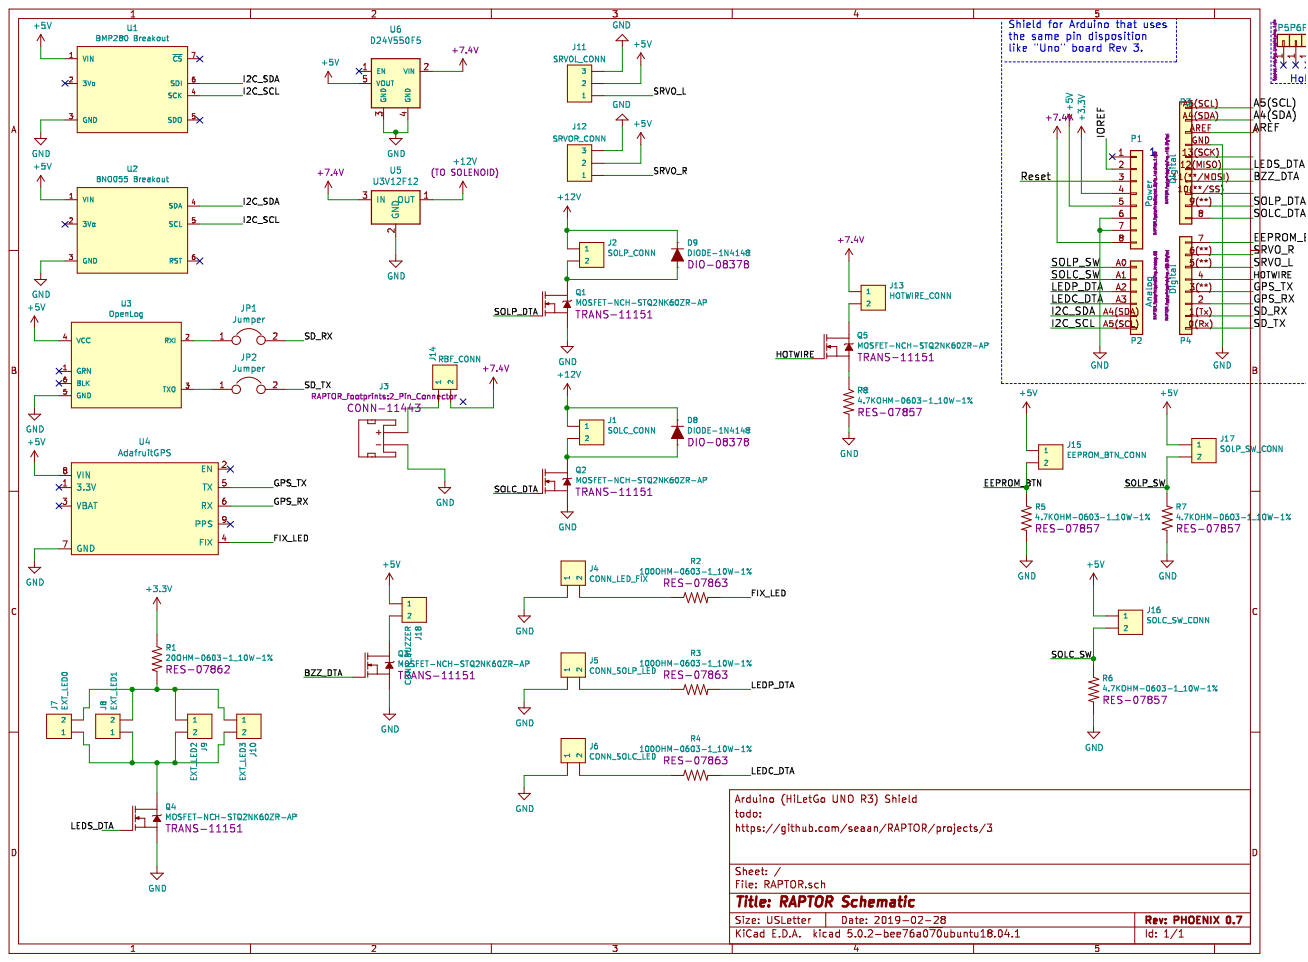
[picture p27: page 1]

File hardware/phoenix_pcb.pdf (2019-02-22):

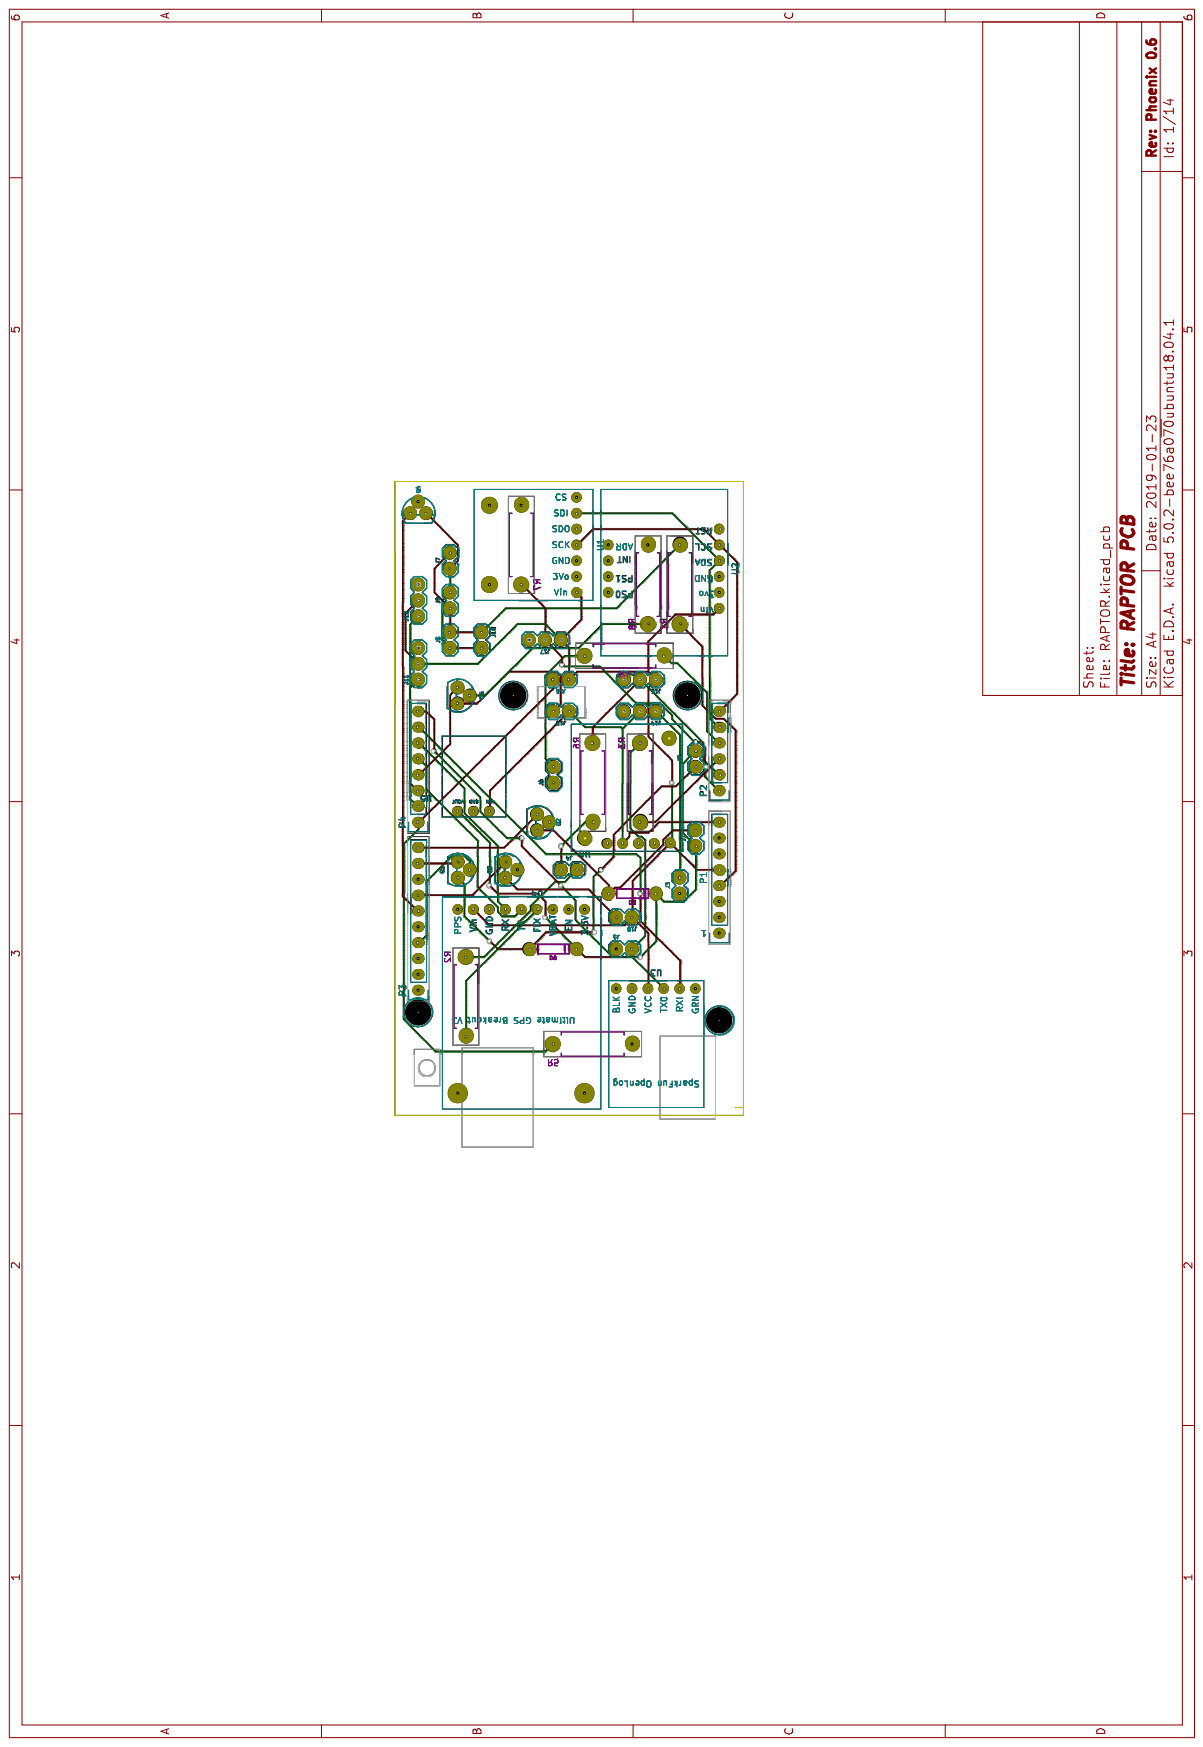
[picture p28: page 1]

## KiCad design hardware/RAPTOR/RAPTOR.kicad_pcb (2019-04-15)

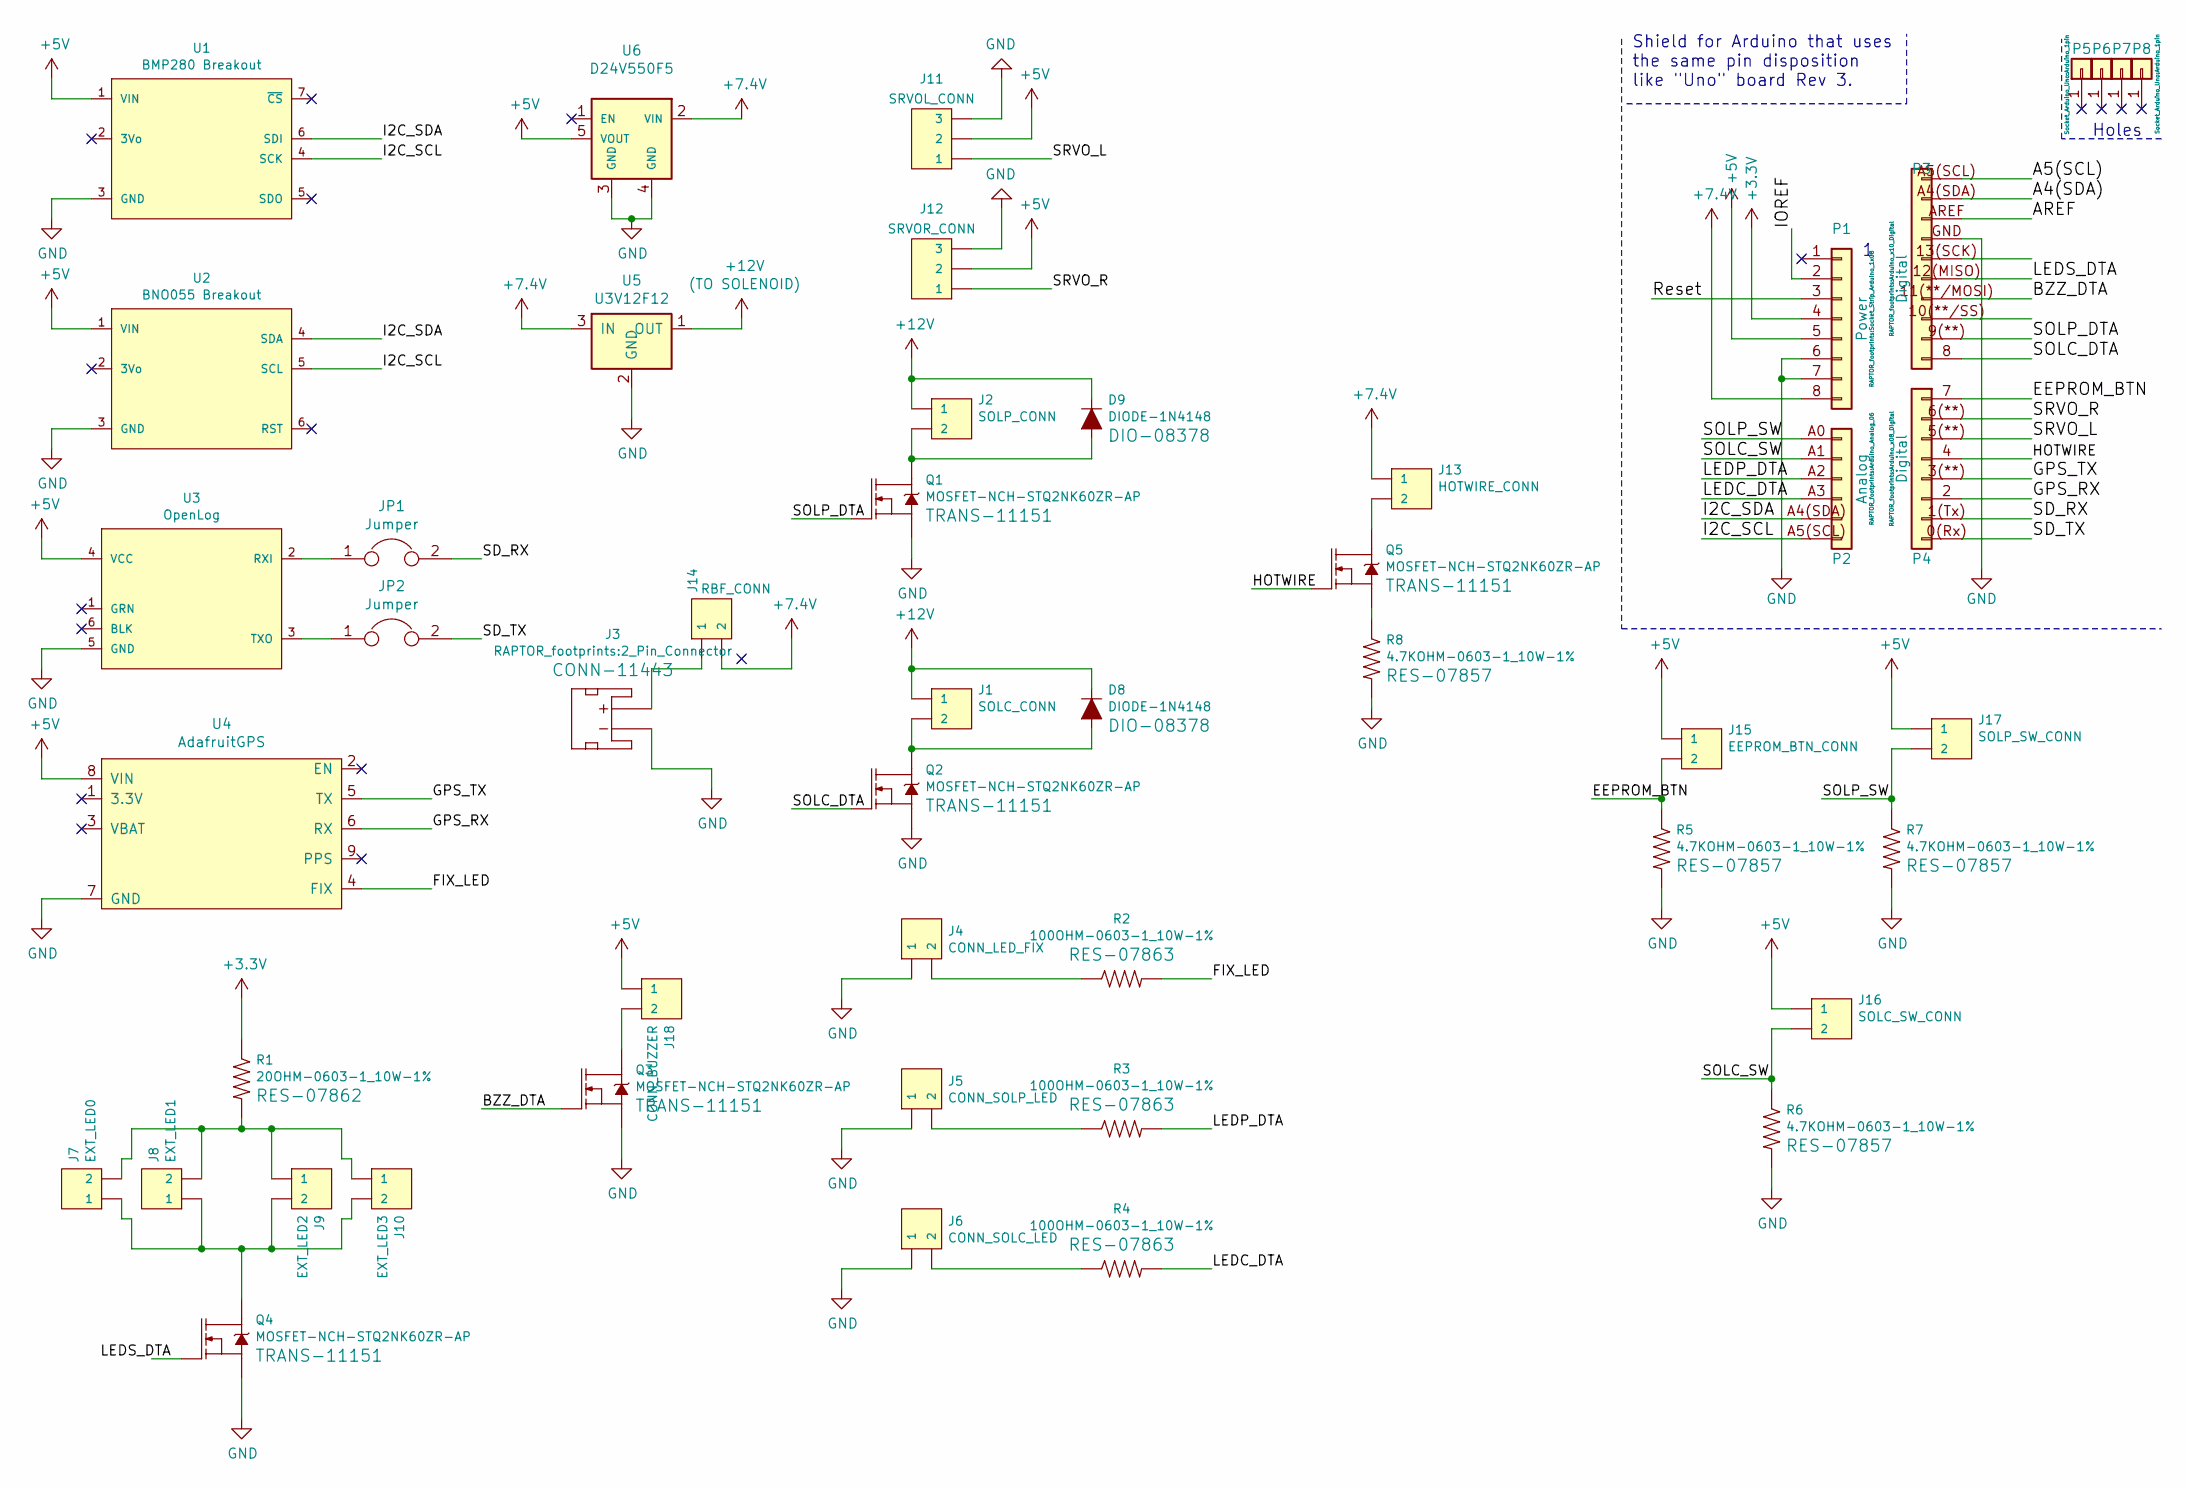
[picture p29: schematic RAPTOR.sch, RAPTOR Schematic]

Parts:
D8, D9: DIODE-1N4148
J1: SOLC_CONN; Molex-2pin
J2: SOLP_CONN; Molex-2pin
J3: JST_2MM_MALE; 2_Pin_Connector
J4: CONN_LED_FIX; Molex-2pin
J5: CONN_SOLP_LED; Molex-2pin
J6: CONN_SOLC_LED; Molex-2pin
J7: EXT_LED0; Molex-2pin
J8: EXT_LED1; Molex-2pin
J9: EXT_LED2; Molex-2pin
J10: EXT_LED3; Molex-2pin
J11: SRVOL_CONN; Molex-MOTOR
J12: SRVOR_CONN; Molex-MOTOR
J13: HOTWIRE_CONN; Molex-2pin
J14: RBF_CONN; Molex-2pin
J15: EEPROM_BTN_CONN; Molex-2pin
J16: SOLC_SW_CONN; Molex-2pin
J17: SOLP_SW_CONN; Molex-2pin
J18: CONN_BUZZER; Molex-2pin
JP1, JP2: Jumper
P1: Power; Socket_Strip_Arduino_1x08
P2: Analog; Arduino_Analog_06
P3: Digital; Arduino_x10_Digital
P4: Digital; Arduino_x08_Digital
P5, P6, P7, P8: CONN_01X01; Arduino_1pin
Q1, Q2, Q3, Q4, Q5: MOSFET-NCH-STQ2NK60ZR-AP; MOSFET
R1: 20OHM-0603-1_10W-1%; Resistor
R2, R3, R4: 100OHM-0603-1_10W-1%; Resistor
R5, R6, R7, R8: 4.7KOHM-0603-1_10W-1%; Resistor
U1: BMP280 Breakout; BMP280
U2: BNO055 Breakout; BNO055
U3: OpenLog
U4: AdafruitGPS
U5: U3V12F12
U6: D24V550F5; D24v50f5_Reg

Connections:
+3V3: P1.4, R1.1
+5V: J11.2, J12.2, J15.1, J16.1, J17.1, J18.1, P1.5, U1.1 (VIN), U2.1 (VIN), U3.4 (VCC), U4.8 (VIN), U6.5 (VOUT)
+7.5V: J13.1, J14.2, P1.8, U5.3 (IN), U6.2 (VIN)
+12V: D8.C, D9.C, J1.1, J2.1, U5.1 (OUT)
/A4(SDA): P3.A4(SDA)
/A5(SCL): P3.A5(SCL)
/AREF: P3.AREF
/BZZ_DTA: P3.11(**/MOSI), Q3.1 (G)
/EEPROM_BTN: J15.2, P4.7, R5.1
/FIX_LED: R2.2, U4.4 (FIX)
/GPS_RX: P4.2, U4.6 (RX)
/GPS_TX: P4.3(**), U4.5 (TX)
/HOTWIRE: P4.4, Q5.1 (G)
/I2C_SCL: P2.A5(SCL), U1.4 (SCK), U2.5 (SCL)
/I2C_SDA: P2.A4(SDA), U1.6 (SDI), U2.4 (SDA)
/IOREF: P1.2
/LEDC_DTA: P2.A3, R4.2
/LEDP_DTA: P2.A2, R3.2
/LEDS_DTA: P3.12(MISO), Q4.1 (G)
/Reset: P1.3
/SD_RX: JP1.2, P4.1(Tx); also elsewhere on the board
/SD_TX: JP2.2, P4.0(Rx); also elsewhere on the board
/SOLC_DTA: P3.8, Q2.1 (G)
/SOLC_SW: J16.2, P2.A1, R6.1
/SOLP_DTA: P3.9(**), Q1.1 (G)
/SOLP_SW: J17.2, P2.A0, R7.1
/SRVO_L: J11.1, P4.5(**)
/SRVO_R: J12.1, P4.6(**)
GND: J3.1 (-), J4.1, J5.1, J6.1, J11.3, J12.3, P1.6, P1.7, P3.GND, Q1.2 (S), Q2.2 (S), Q3.2 (S), Q4.2 (S), R5.2, R6.2, R7.2, R8.2, U1.3 (GND), U2.3 (GND), U3.5 (GND), U4.7 (GND), U5.2 (GND), U6.3 (GND), U6.4 (GND)
unnamed: D8.A, J1.2, Q2.3 (D)
unnamed: D9.A, J2.2, Q1.3 (D)
unnamed: J4.2, R2.1
unnamed: J5.2, R3.1
unnamed: J6.2, R4.1
unnamed: J7.2, J8.2, J9.1, J10.1, R1.2
unnamed: J7.1, J8.1, J9.2, J10.2, Q4.3 (D)
unnamed: J13.2, Q5.3 (D)
unnamed: J3.2 (+), J14.1
unnamed: J18.2, Q3.3 (D)
unnamed: Q5.2 (S), R8.1
unnamed 47: JP1.1, U3.2 (RXI); also elsewhere on the board
unnamed 48: JP2.1, U3.3 (TXO); also elsewhere on the board

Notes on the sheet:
Holes
Shield for Arduino that uses the same pin disposition like "Uno" board Rev 3.

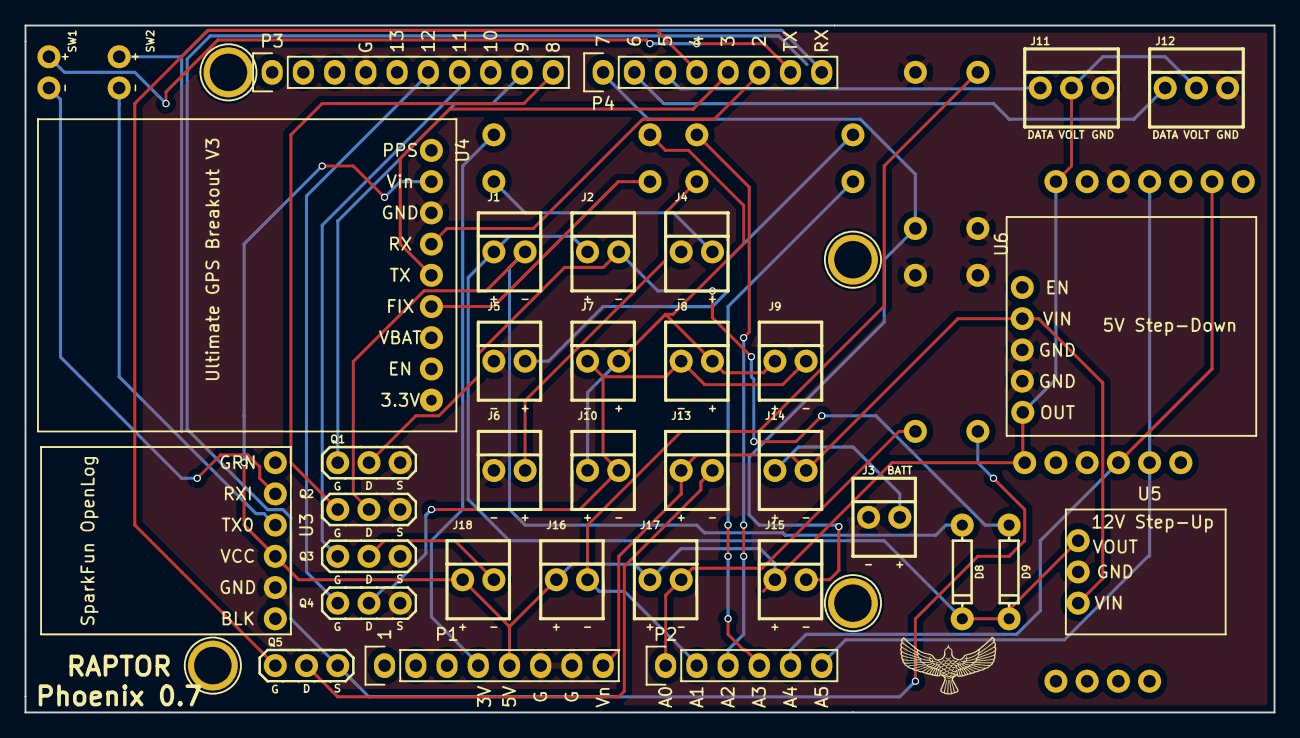
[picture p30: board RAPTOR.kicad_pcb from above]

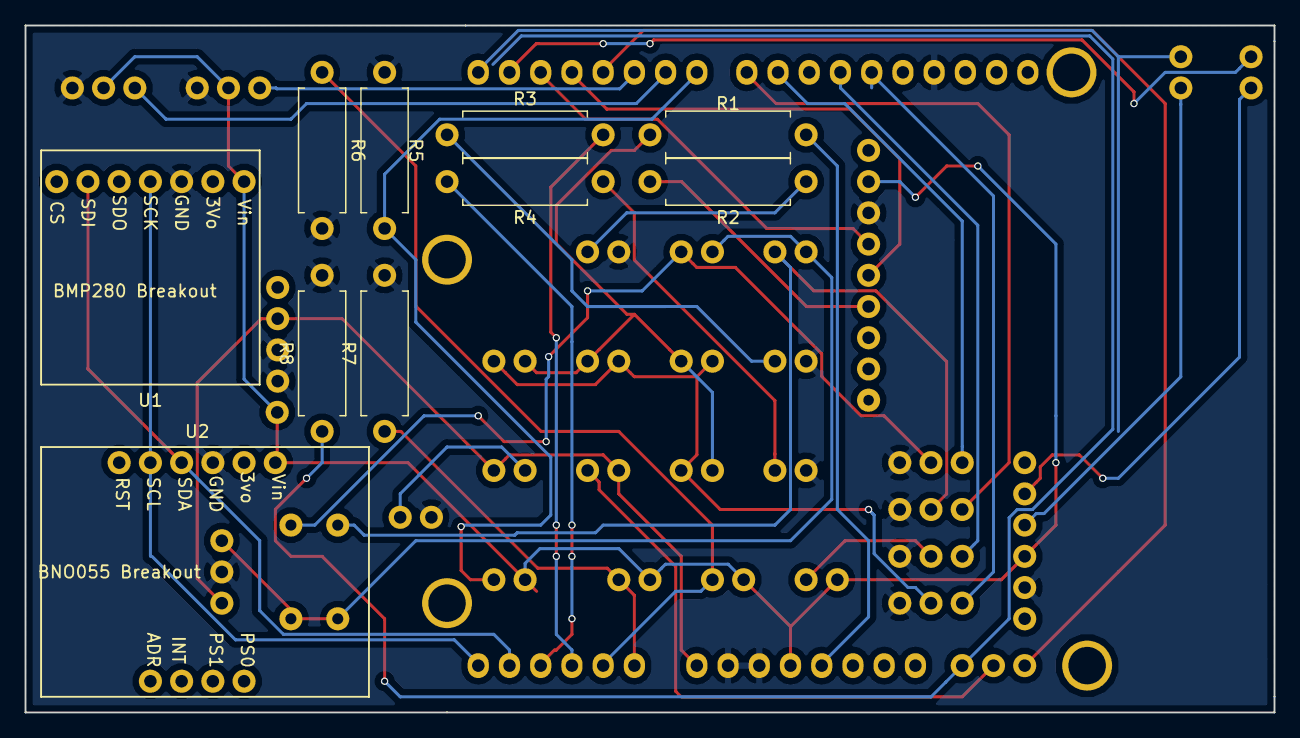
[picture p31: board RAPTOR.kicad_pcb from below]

Board: 2 copper layers, 101.6 x 55.9 mm, 49 parts (10 on the bottom side), 37 nets.

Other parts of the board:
SW1, SW2: SW_Push_Open; Jumper

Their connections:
/SD_RX: SW1.2; also elsewhere on the board
/SD_TX: SW2.2; also elsewhere on the board
unnamed 47: SW1.1; also elsewhere on the board
unnamed 48: SW2.1; also elsewhere on the board

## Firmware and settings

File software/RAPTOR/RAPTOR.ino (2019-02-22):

#include <elapsedMillis.h>
#include <EEPROM.h>
#include <Streaming.h> // http://arduiniana.org/libraries/streaming/

#include "src/guidance/pilot/pilot.h"
#include "src/environment/environment.h"
#include "src/guidance/drivers/solenoid/solenoid.h"

#define GROUND_ALT 15.24  // altitude to transition to FS1 [ASCENT] or FS3 [LANDED], =50ft
#define CUTDOWN_ALT 609.6 // altitude to transition to FS2 [DESCENT], =1000ft

#define TARGET_LONG -86.633730
#define TARGET_LAT 34.722988 // HARD CODED TARGET COORDINATES

#define DEPLOY_DELAY 1200 // time to wait between deployment and guidance [ms]
#define FLY_DELAY 1000    // time to wait between calling fly [ms]

#define BZZ_DTA 11  // buzzer
#define LEDS_DTA 12 // external flight LEDs

#define SET_BTN 7 // eeprom write button

Environment environment; // contains all of our sensors in one nice class
Pilot pilot;             // takes environmental input and makes all decisions regarding flight control

uint8_t flight_state = 0; // current flight state
long fly_time = 0;        // amount of time passed between flight controlling
bool didwake = false;     // whether or not we have woken the pilot yet

/* 
 * Arduino setup function, first function to be run.
 */
void setup()
{
  environment.time_elapsed = 0;

  /* Buzzer and LEDs */
  pinMode(BZZ_DTA, OUTPUT);  // Set buzzer to output
  pinMode(LEDS_DTA, OUTPUT); // Set LEDs to output

  Serial.begin(9600);

  pinMode(SET_BTN, OUTPUT);
  if (!digitalRead(SET_BTN))
  {
    read_EEPROM();
  }
  /* Solenoids, Servos, BMP, BNO */
  startup_sequence();

  if (digitalRead(SET_BTN))
  {
    write_EEPROM();
  }

  /* GPS */
  environment.gps->init();

  delay(10);
  Serial.print(F("TIME,"
                 "TEMPERATURE,PRESSURE,ALTITUDE,"
                 "LATITUDE,LONGITUDE,ANGLE,GPS_ALT,"
                 "X,Y,Z, "
                 "SWC,SWP,"
                 "TURN,FLIGHT_STATE\n")); // data header
}

/* 
 * arduino loop function, always runs.
 */
void loop()
{
  switch (flight_state)
  {
  // FS0 [LAUNCH]
  case 0:
    environment.bmp->update();

    if (environment.bmp->altitude > GROUND_ALT)
    { // at 50ft (15.24 meters), transition to FS1 [ASCENT]
      flight_state = 1;
      write_EEPROM();
    }

    // blink the LEDs and print data at a rate of 1Hz
    blink_led(1000);
    print_data();
    break;

  // FS1 [ASCENT]
  case 1:
    environment.bmp->update();

    if (environment.bmp->altitude > CUTDOWN_ALT)
    { // at the cutdown altiude perform cutdown, deploy, and transition to FS2 [DESCENT]
      // CUTDOWN
      cutdown();

      if (!cutdown_switch())
      { // we want to make sure that we have cut down
        Serial << F("\n!!!! CUTDOWN ERROR DETECTED !!!!\n");
        cutdown(); // try cutdown again, probably won't do much
      }

      // PARAFOIL DEPLOY
      while (environment.bmp->altitude > CUTDOWN_ALT - 3.048)
      { // wait 3 meters to deploy the parafoil
        delay(1);
        environment.bmp->update();
        print_data();
      }

      parafoil_deploy();

      if (parafoil_switch())
      { // make sure the parafoil has deployed
        Serial << F("\n!!!! PARAFOIL DEPLOYMENT ERROR DETECTED !!!!\n");
        parafoil_deploy(); // try deploying parafoil again, probably won't do much
      }

      delay(DEPLOY_DELAY); // wait for the parafoil to deploy/inflate before we begin guidance

      flight_state = 2;
      write_EEPROM();
    }

    // blink the LEDs and print data at a rate of 5Hz
    blink_led(200);
    print_data();
    break;

  // FS2 [DESCENT]
  case 2:

    // if we have yet to wake the pilot, do so
    if (!didwake)
    {
      // first set up our coordinates
      Coordinate current, target;

      current.latitude = environment.gps->latitude;
      current.longitude = environment.gps->longitude;

      target.latitude = TARGET_LAT;
      target.longitude = TARGET_LONG;

      // then wake the pilot and give it the coordinates
      Serial << "Waking pilot\n";
      pilot.wake(current, target);
      didwake = true;
    }

    environment.bmp->update();

    fly_time = timeElapsed;
    if (fly_time > FLY_DELAY)
    {                                    // don't want to constantly call fly
      pilot.fly(environment.gps->angle); // the pilot just needs our current angle to do his calculations
      fly_time = 0;
    }

    if (environment.bmp->altitude < GROUND_ALT)
    { // at 50ft (15.24 meters), transition to FS3 [LANDED]
      if (environment.landing_check())
      { // make sure that we have landed by checking the altitude constantly
        pilot.sleep();
        flight_state = 3;
        Serial << "\n!!!! LANDED !!!!\n";
      }
    }

    // blink the LEDs and print data at 10Hz
    blink_led(100);
    print_data();
    break;

  // FS3 [LANDED]
  case 3:
    // in the landed state, only toggle the LEDs and buzzer every 2 seconds, then print data
    analogWrite(BZZ_DTA, 200);
    blink_led(2000);
    analogWrite(BZZ_DTA, 0);

    delay(200);
    print_data();

    break;
  }
}

/*
 * print_data updates sensor readings then prints all relevant data to the serial pins.
 */
void print_data()
{
  environment.update();

  /* Let's spray the serial port with a hose of data */

  // time, temperature, pressure, altitude,
  Serial << time_elapsed << F(",") << environment.bmp->temperature << F(",") << environment.bmp->pressure
         << F(",") << environment.bmp->altitude << F(",");

  // latitude, longitude, angle, (gps) altitude,
  Serial << _FLOAT(environment.gps->latitude, 7) << F(",") << _FLOAT(environment.gps->longitude, 7)
         << F(",") << _FLOAT(environment.gps->angle, 7) << F(",") << environment.gps->altitude << F(",");

  // x orientation, y orientation, z orientation,
  Serial << _FLOAT(environment.bno->data.orientation.x, 4) << F(",") << _FLOAT(environment.bno->data.orientation.y, 4)
         << F(",") << _FLOAT(environment.bno->data.orientation.z, 4) << F(",");

  // cutdown switch, parafoil switch, turn status, flight state
  Serial << cutdown_switch() << F(",") << parafoil_switch() << F(",")
         << pilot.get_turn() << F(",") << flight_state << "\n"; // write everything to SD card
}

/* 
 *  startup_sequence intitializes our solenoids, servos, and sensors.
 *   If in flight state 0 (launch), performs a sequence that indicates board power,
 *   solenoid power, servo power, and successful sensor initialization.
 */
void startup_sequence(void)
{
  // indicate board power with a buzzer beep if in flight state 0
  if (flight_state == 0)
  {
    analogWrite(BZZ_DTA, 200); // turn on the buzzer for half a second
    delay(500);
    analogWrite(BZZ_DTA, 0);
  }

  // intialize solenoids, should hear them click and see the indicator LEDs turn on
  sol_init();
  cutdown_switch();
  parafoil_switch();

  // initialize servos, if we're in flight state 0 we'll test them as well
  pilot.servo_init();
  if (flight_state == 0)
  {
    pilot.servo_test(); // rotates and resets each servo
    delay(200);
  }

  // initialize sensors, then indicate if we were successful or not
  if (environment.init(flight_state))
  { // if the initialization was successful and we're in flight state 0 blink 5 times
    if (flight_state == 0)
    {
      for (int i = 0; i < 5; i++)
        blink_led(500);
    }
  }
  else
  { // if the initialization was unsucessful and we're in flight state 1 blink 15 times
    if (flight_state == 0)
    {
      for (int i = 0; i < 15; i++)
      {
        analogWrite(BZZ_DTA, 200);
        blink_led(500);
        analogWrite(BZZ_DTA, 0);
      }
    }
  }
}

/* 
 * write_EEPROM deposits flight state and baseline pressure into the EEPROM. 
 */
void write_EEPROM()
{
  EEPROM.put(0, flight_state);                // flight state is always at address 0
  EEPROM.put(100, environment.bmp->baseline); // baseline pressure always at address 100
}

/* 
 * read_EEPROM retrieves flight state and baseline pressure from the EEPROM. 
 */
void read_EEPROM()
{
  Serial << "Read EEPROM\n";

  // retrive flight state from address 0
  EEPROM.get(0, flight_state);
  if (flight_state == 1)
    flight_state = 2; // if the read flight state is 1, transition immediately to 2 as the solenoids fail open

  // retrieve baseline pressure from address 100
  EEPROM.get(100, environment.bmp->baseline);

  // print retrieved data
  Serial << "Saved flight state: " << flight_state;
  Serial << "\nSaved baseline: " << environment.bmp->baseline << "\n";
}

/* 
 * blink_led toggles the LED, then delays for a certain length of time.
 *  Can be used to achieve a blink rate, but will delay the entire execution.
 */
void blink_led(int length)
{
  digitalWrite(LEDS_DTA, !digitalRead(LEDS_DTA));
  delay(length);
}

/*
 * custom_angle returns an angle parsed from user input 
 */
float custom_angle(void)
{
  Serial << "\nPlease input an angle: ";
  while (Serial.available() == 0)
    ; // wait for user input
  float angle = Serial.parseFloat();
  Serial << "\nAngle: " << angle << "\n";
  return angle;
}

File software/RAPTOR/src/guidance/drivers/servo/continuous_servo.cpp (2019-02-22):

/*

*/
#include "continuous_servo.h"
#include <Arduino.h>

/* Public Methods */
/*
 *	turn will rotate the servos to a certain configuration, based on the set time to rotate (TTR),
 * 		if reset is given as true, the servo will rotate in the opposite direction for the same amount of time.
 */
void ContinuousServo::turn(bool reset /*= false*/)
{
	this->attach(this->pin);
	this->writeMicroseconds(STOP); // Stop the servos just in-case they're running already.
	delay(10);
	if (servo == RIGHT)
	{
		if (reset)`
			this->writeMicroseconds(CCW);
		else
			this->writeMicroseconds(CW); // based on the turn, we will rotate CW or CCW
	}
	else
	{ // left servo
		if (reset)
			this->writeMicroseconds(CW); // reset will turn the servo the other way for the same amount of time
		else
			this->writeMicroseconds(CCW);
	}
	delay(TTR);

	this->writeMicroseconds(STOP); // Stop the servos once we've reached the deflection setting.
	delay(100);
	this->detach();
}

/*
 *	reset will reset the servos to the default position after a turn.
 */
void ContinuousServo::reset()
{
	turn(true);
}

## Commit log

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2018-04-16 fix compile errors, add BMP180 functionality
    [RAPTOR.ino]
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2018-04-21 pre-test flight code fixes
    [RAPTOR.ino]
2018-04-24 flight one data + python analysis
    graphs created using matplotlib
    [DATA.csv, DATA2.csv]
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2018-09-03 8-31 flight data analysis, fix pathfinder, add pseudocode
    fixed pathfinder angle to be positive bearing as if on a compass
    analyzed data from 8-31 flight
    created pseudocode for flight 3
    [4-21_DATA.csv, 8-31_DATA.CSV, 8-31_DATA_fixed.CSV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]
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2018-09-09 Added code for altitude correction
    [RAPTOR.ino]
2018-09-14 fix BZZ_DTA pin
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2018-09-14 Correct pilot and pathfinder for current ideas
    [Pilot.cpp]
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2018-09-15 replace BMP library, add externs to fix linkage errors
    [RAPTOR.ino]
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2018-09-17 add cutdown logic, seperate correct alt to ascending and descending
    [RAPTOR.ino, solenoid.cpp]
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2018-09-17 implement streaming operators, fix function headers
    [RAPTOR.ino, solenoid.cpp]
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2018-09-19 servo fixes
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2018-09-21 test and fix servo adjustments
    [Pilot.cpp, RAPTOR.ino]
2018-09-21 fix servo pins
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2018-09-23 add startup sequence comments, resolves #6
    [RAPTOR.ino]
2018-09-27 Simupy (#16)
    * add py file
    * read serial input
    * test input and printing
    * testing
    * use legacy code
    * test with file, edit for arduino use
    * remove comment
    * add line verification
    * debugging
    * fixed!
    * update documentation
    * remove print_data changes
    [RAPTOR.ino, simu.py, simufile.py]
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2018-10-03 add error handling for zero'd altitudes, resolves #25
    [RAPTOR.ino]
2018-10-03 add landing check, resolves #24
    [RAPTOR.ino]
2018-10-03 formatting, revert some testing specific modfiications
    [Pilot.cpp, RAPTOR.ino, continuous_servo.cpp]
2018-10-05 move pilot wake, resolves #23
    [RAPTOR.ino]
2018-10-05 test deflection setting, debug find turn, resolves #26 resolves #29
    [Pilot.cpp, RAPTOR.ino]
2018-10-05 full systems test resolves #22
    [RAPTOR.ino]
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2018-10-09 correct to accurate data header
    [RAPTOR.ino]
2018-10-09 simplify and refactor pathfinder, resolve #36
    [Pilot.cpp]
2018-10-09 add environment update, resolve #32
    [RAPTOR.ino]
2018-10-17 Converts BMP data to meters as well as all references to altitude . Resolves issue #40.
    [RAPTOR.ino]
2018-10-25 new project from arduino uno template
    [hardware.kicad_pcb, hardware.sch]
2018-10-25 Revert "new project from arduino uno template"
    This reverts commit d8d94c75d211f8ad6141b76f4c75afd9c963bf61.
    [hardware.kicad_pcb, hardware.sch]
2018-10-25 create project from arduino mega template with gitignore
    [RAPTOR.kicad_pcb, RAPTOR.sch]
2018-10-25 add BMP280 and wiring
    [RAPTOR.sch]
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2018-10-26 create hardware, software, flight folders
    [4-21_DATA.csv, 8-31_DATA.CSV, 8-31_DATA_fixed.CSV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]
2018-10-26 add bmp footprint to pcb
    [RAPTOR.kicad_pcb]
2018-10-26 move to uno, re-add bmp
    [RAPTOR.kicad_pcb, RAPTOR.sch]
2018-10-26 add bno, start on footprint for bmp
    [RAPTOR.sch]
2018-10-27 correct location, add gps alt print
    [RAPTOR.ino]
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2018-10-30 resolves #49 on line 109
    [RAPTOR.ino]
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2018-10-30 add inflation delay, resolves #49
    [RAPTOR.ino]
2018-11-03 Attempted to Change the Bno005 Footprint - didn't go well
2018-11-03 small changes to gps symbol, add gps and openlog to schematic
    [RAPTOR.sch]
2018-11-06 fixed naming of the open log files and include the SoftwareSerial library from arduino
    [openlog.cpp]
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2018-11-08 add print to deploy while, resolves #50
    [RAPTOR.ino]
2018-11-10 Added all the footprints and associated them with the symbols in the schematics
    [RAPTOR.kicad_pcb, RAPTOR.sch]
2018-11-10 fix sensor numbers, add servos, solenoids, leds, switches
    [RAPTOR.sch]
2018-11-10 add net + pcb files
    [RAPTOR.kicad_pcb, RAPTOR.sch]
2018-11-13 add delay after buzz
    [RAPTOR.ino]
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2019-01-12 First upload of CAD files
    [Caliper Release CutDown.cfg, Parafoil X-frame center v2.stl, Parafoil X-frame center.stl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]
2019-01-12 Add voltage regulators, schematic pdf
    [RAPTOR.sch]
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2019-01-12 Reorganized all of the CAD files for Phoenix
    [Arduino_Uno_bumper_fixedV2.0.stl, Arm.stl, Brake line controller assembly.cfg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]
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2019-01-12 Added GoPro files and GoPros to the assembly
    [PhoenixAssembly.cfg]
2019-01-12 Voltage Reg Footprints
    Created the voltage regulator footprint for he 12v reg
    [RAPTOR.sch]
2019-01-12 Auto stash before merge of "hardware" and "origin/hardware"
    [RAPTOR.sch]
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2019-01-12 mosfet source to gnd + sol net label, removed second vreg
    Mosfet was hooked up to -12V, instead added a GND connection and in the middle of source and ground put a wire with a diode going out to a SOLP/C connection. Removed redundant voltage regulator (<0.7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
    [RAPTOR.sch]
2019-01-15 resolves #57
    [RAPTOR.sch, _saved_RAPTOR.sch]
2019-01-15 change battery to battery connector
    [RAPTOR.sch]
2019-01-15 resolves #56
    [RAPTOR.sch]
2019-01-15 add pulldown res, resolves #58
    [RAPTOR.sch]
2019-01-15 add molex connectors for LEDs
    [RAPTOR.sch]
2019-01-15 Customize Arduino Connectors, add names to net labels, resolve #59
    replace motors with molex connectors
    [RAPTOR.sch]
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2019-01-17 moved a single mosfet
    [RAPTOR.sch]
2019-01-17 Add Parafoil Attachment Mech to Phoenix Assembly
    [Parafoil_Attachment_Mech.cfg, PhoenixAssembly.cfg]
2019-01-17 Fixed MOSFETS gate and drain on diagram
    [RAPTOR.sch]
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2019-01-17 change LED resistor values
    [RAPTOR.sch]
2019-01-17 add a hotwire
    Needs correct labeling
    [RAPTOR.sch]
2019-01-18 fix hotwire
    [RAPTOR.sch]
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2019-01-18 added connectors for exterior LEDs in place of diodes
    [RAPTOR.sch]
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2019-01-18 remove capacitors from circuit
    [RAPTOR.sch]
2019-01-18 put stuff on pcb thing
    [RAPTOR.kicad_pcb, RAPTOR.sch]
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2019-01-19 Fitted parts
    Placed all the compnents on the actual PCB not just off to the side
    [RAPTOR.kicad_pcb, RAPTOR.sch]
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2019-01-19 PCB Error Fixing
    Changed footprints and symbols to be more accurate
    [RAPTOR.kicad_pcb, RAPTOR.sch]
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2019-01-21 Test of mergy bois
    ^^^^
    [RAPTOR.kicad_pcb]
2019-01-21 Version 1 of fully wired PCB
    A preliminary full connection of the PCB board
    [RAPTOR.kicad_pcb]
2019-01-23 Widened PCB Board
    This should resolve something but IDK the number
    [RAPTOR.kicad_pcb]
2019-01-23 Revert "Widened PCB Board"
    This reverts commit 6127001810acaa0b6aebb6d9f1e36fbc48228c71.
    [RAPTOR.kicad_pcb]
2019-01-24 Revert "Revert "Widened PCB Board""
    This reverts commit edbbf49bd2c69fdd694dc2b23b572114c8313dd8.
    [RAPTOR.kicad_pcb]
2019-01-24 add connector for buzzer, resolves #72
    [RAPTOR.kicad_pcb, RAPTOR.sch]
2019-01-24 increase resistor footprint length
    [RAPTOR.sch]
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2019-01-24 moved names on silkscreen and remove long names
    [RAPTOR.kicad_pcb]
2019-01-24 Trial Wireng V2
    Im probs gonna chage some stuff here
    [RAPTOR.kicad_pcb]
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2019-01-24 Full Wire and Ground Fill
    Also got dem Vias dig dawg.
    [RAPTOR.kicad_pcb]
2019-01-24 Moved Screw Hole
    Hopefully is in the good spot
    [RAPTOR.kicad_pcb]
2019-01-24 fixed silk-screen names again
    [RAPTOR.kicad_pcb]
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2019-01-26 Changes to parafoil positioning from Bottom to Back of Payload.
    [Parafoil_Attachment_Mech.cfg, PhoenixAssembly.cfg]
2019-01-26 Update Mosfet Vals
    yeet yeet yeet yoote yeet yeet yeet yeet yoote yeet yeet yeet yeet yoote yeet yeet yeet yeet yoote yeet yeet yeet yeet yoote yeet
    [RAPTOR.kicad_pcb, RAPTOR.sch]
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2019-01-26 Took racy pictures of the PCB
    Don't let them leak to the internet it could ruin her professional career
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2019-02-11 Added CAD files for the PCB assembled with an Arduino Uno
    [Pin Header 1x1 TH Pitch 2.54mm.stp, Pin Header 1x10 TH Pitch 2.54mm.stp, Pin Header 1x11 TH Pitch 2.54mm.stp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]
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2019-02-22 New Mechanical Release for Actual Parts
    There are 4 new parts files, 1 new assembly file, and a modified Solenoid file.
    [CaliperReleaseCutDownActual.cfg]
2019-02-26 Added STL Files for Printing of Bow Release
    [Base_2.stl, ConnectingArm_2.stl, TriggerCover_2.stl]
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2019-02-28 3 pin to 2 pin, resolve #90
    [RAPTOR.sch]
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2019-02-28 move R2 and R3, resolves #88
    [RAPTOR.kicad_pcb]
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2019-02-28 add 2 pin molex and motor silkscreen, resolves #92
2019-02-28 fix molex footprints
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2019-03-01 All Routed w/o RXTX button
    All the connections are made except for the rx and tx button
    [RAPTOR.kicad_pcb]
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2019-03-01 Finished Roouting
    Needs checking though. Full error and netlist tests
    [RAPTOR.kicad_pcb]
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2019-03-01 flip some + and - signs
    [RAPTOR.kicad_pcb]
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2019-03-04 Updated Base of Bow Release, added STL files for printing
    [Base_2.stl, CaliperReleaseCutDownActual.cfg, Chamfer Edge UpgradeMotor and Wheel Frame NO SUPORRT.stl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]
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2019-03-29 Updated Base of Bow Release, added STL files for printing
    Change to Base, adjust Base 2 file location for solenoid
    [Base_2.stl, CaliperReleaseCutDownActual.cfg, Chamfer Edge UpgradeMotor and Wheel Frame NO SUPORRT.stl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]
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2019-04-12 Mechanical Update 4/11
    Add Connecting rod 4A and 4B for 45 degrees solenoid offset. Updated Base 3.
    [BowReleaseCutDown_Rev2.cfg, PhoenixAssembly.cfg]
2019-04-13 Mechanical Update 4/13
    Adjust Primary Cutdown Assembly, added ConnectingArm 4A and 4B. Modified ConnectingArm4A, adjusting for width of trigger.
    [BowReleaseCutDown_Rev2.cfg, ConnectingArm_4A.stl]
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2019-08-24 Mechanical Update 8/24/19
    Add Single Servo Mount asm
    [Axis-holder v2.step, Servo Futaba S3003 v6.iges, Servo Futaba S3003 v6.step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]
